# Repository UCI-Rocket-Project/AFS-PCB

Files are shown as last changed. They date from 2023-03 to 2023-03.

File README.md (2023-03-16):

# UCIRP Avionics Flight Sensor (AFS)
v1.1 "Rigel" (a star in Orion's constellation)

The board includes: 
- [Adafruit BMP388](https://www.amazon.com/Adafruit-BMP388-Precision-Barometric-Altimeter/dp/B07JXYK9ZB) Barometric and Pressure Sensor
- [Hitlego MPU-6050](https://www.amazon.com/HiLetgo-MPU-6050-Accelerometer-Gyroscope-Converter/dp/B01DK83ZYQ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) Accelerometer and Gyroscope
- [Adafruit Ultimate GPS](https://www.adafruit.com/product/746#description)
- [Digi XBee-PRO XSC S3B](https://www.mouser.com/ProductDetail/Gravitech/XBee-USB?qs=Vxac6xGyzPnMlpwH9hhfHQ%3D%3D) 
- [Sparkfun XBee Adapter](https://www.sparkfun.com/products/11373)
- Teensy 4.1
- [Linear Regulator (9V -> 5V)](https://www.digikey.com/en/products/detail/stmicroelectronics/L7805CV/585964)

Communication Protocols Used:
| Component  | Communication Protocol | 
| --- | --- |
| BMP388  | SPI  | 
| ECU 1.5 "Orion" | I2C (Wire) |
| GPS  | UART (Serial 2) |
| MPU-6050  | I2C (Wire 1)  |
| SD Module | SPI |
| XBEE  | UART (Serial 6) |

Pinouts:

BMP
- CS	 -> 10 CS
- SDI  -> 11 MOSI
- SDO  -> 12 MISO
- SCK  -> 13 SCK

ECU 1.5 "Orion"
- SDA2  -> 18 SDA
- SCL2  -> 19 SCL

GPS (Serial2 port in Teensy 4.1)
- TX	 -> 7 RX2
- RX	 -> 8 TX2

MPU (Wire1 port in Teensy 4.1)
- SDA  -> 17 SDA1
- SCL	 -> 16 SCL1

SD Module 
- MISO -> 39 MISO1
- MOSI -> 26 MOSI1
- SCK  -> 27 SCK1
- CS   -> 38 CS1

XBEE (Serial6 port in Teensy 4.1)
- DOUT -> 25  RX6
- DIN  -> 24 TX6

## Used Packages
- Teensy 4.1 [symbol](https://github.com/XenGi/teensy_library) and [footprint](https://github.com/XenGi/teensy.pretty). Related files and license is located under `/teensylib`.

## Notes
- The board requires an external 9V battery to power sensors and the Teensy. The onboard regulator will step down to 5V and provide stable 5V power.
- The GPS uses an optional "CR1220 coin cell to keep the RTC running and allow warm starts"
- The XBee module (not on AFS PCB) mounts on top of the XBee USB adapter. The USB adapter board has power and serial pass-through to the XBee module
- The board was renamed from "Avionics Test Payload (ATP)" to "Avionics Flight Sensor (AFS)"

### v1.1
- Changed [Adafruit XBee USB Adapter](https://www.adafruit.com/product/247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) to [Sparkfun XBee Adapter](https://www.sparkfun.com/products/11373)
- XBee receives 5V from regulator, instead of 3.3V from Teensy. During testing we found out that Teensy did not supply enough power for Xbee communication and after sending 1 or 2 packages of data, the Teensy would stop working.
- Regulator is flipped, so we can attach a heat sink

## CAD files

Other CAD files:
atp_teensy.wrl.SLDPRT

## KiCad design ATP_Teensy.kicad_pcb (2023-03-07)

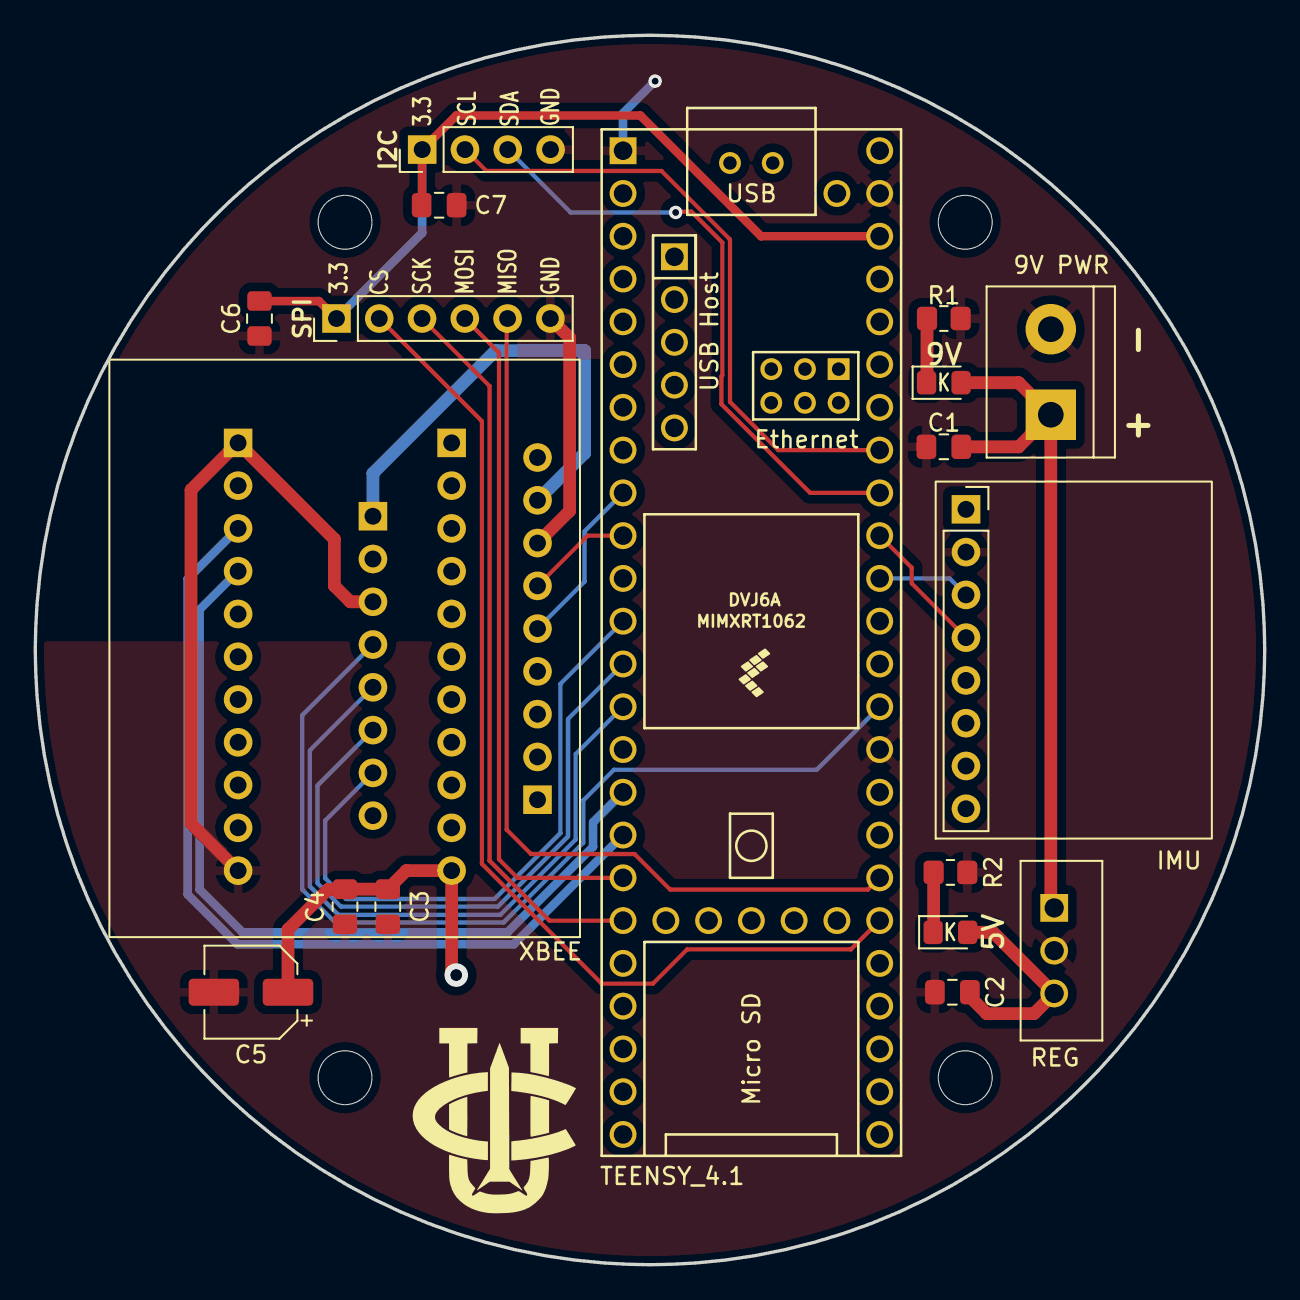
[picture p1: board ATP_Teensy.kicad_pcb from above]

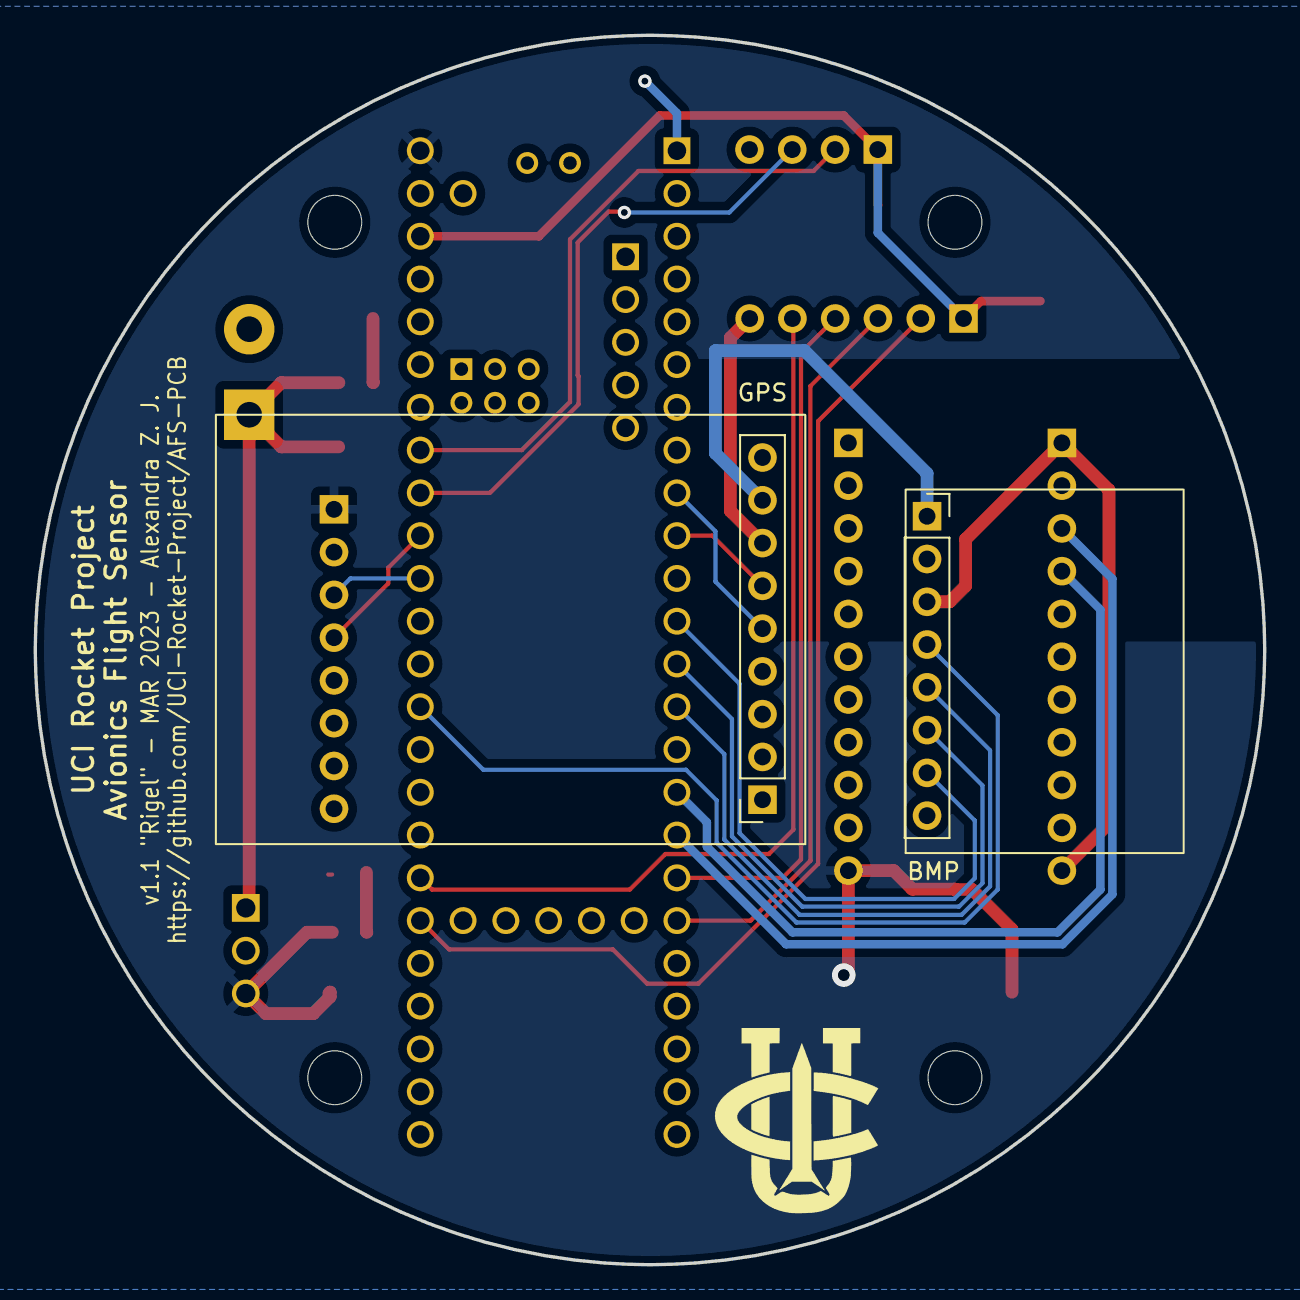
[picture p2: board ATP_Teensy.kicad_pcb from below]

Board: 2 copper layers, 73.0 x 73.0 mm, 26 parts (3 on the bottom side), 22 nets.

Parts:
5V, 9V: LED; LED_0805_2012Metric_Pad1.15x1.40mm_HandSolder
9V PWR: Screw_Terminal_01x02; TerminalBlock_bornier-2_P5.08mm
BMP: BMP388_3966; BMP_board
C1, C2: 10nF; C_0805_2012Metric_Pad1.18x1.45mm_HandSolder
C3: 47pF; C_0805_2012Metric_Pad1.18x1.45mm_HandSolder
C4, C6, C7: 1uF; C_0805_2012Metric_Pad1.18x1.45mm_HandSolder
C5: 10uF, 50V; CP_Elec_5x5.4
GPS: GPS; GPS_board
Ge: LOGO; UCIRP_logo
Ge#2: LOGO; UCIRP_logo
I2C: Conn_01x04_Male; PinHeader_1x04_P2.54mm_Vertical
IMU: MPU6050; IMU_board
J2, J3, J4, J5: Conn_01x01; MountingHole_3.2mm_M3
R1: 290R; R_0805_2012Metric_Pad1.20x1.40mm_HandSolder
R2: 90R; R_0805_2012Metric_Pad1.20x1.40mm_HandSolder
REG: L7805CV
SPI: Conn_01x06_Male; PinHeader_1x06_P2.54mm_Vertical
TEENSY_4.1: Teensy4.1; Teensy41
XBEE: XBee_SparkfunRegulatedAdapter; XBee_SparkfunAdapter

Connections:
+3.3V: C6.2, C7.2, I2C.1, SPI.1, TEENSY_4.1.46 (3V3)
+5V: 5V.2 (A), BMP.1 (VIN), C2.2, C3.2, C4.2, C5.1, GPS.8 (VIN), IMU.1 (VCC), REG.3 (OUT), TEENSY_4.1.48 (VIN), XBEE.22 (5V_IN)
+9V: 9V.2 (A), 9V PWR.1, C1.2, REG.1 (IN)
BMP_CS: BMP.7 (CS), TEENSY_4.1.12 (10_CS_MQSR)
BMP_SCK: BMP.4 (SCK), TEENSY_4.1.35 (13_SCK_LED)
BMP_SDI: BMP.6 (SDI), TEENSY_4.1.13 (11_MOSI_CTX1)
BMP_SDO: BMP.5 (SDO), TEENSY_4.1.14 (12_MISO_MQSL)
ECU_SCL: I2C.2, TEENSY_4.1.41 (19_A5_SCL)
ECU_SDA: I2C.3, TEENSY_4.1.40 (18_A4_SDA)
GND: 9V PWR.2, BMP.3 (GND), C1.1, C2.1, C3.1, C4.1, C5.2, C6.1, C7.1, GPS.7 (GND), I2C.4, IMU.2 (GND), R1.2, R2.2, REG.2 (GND), SPI.6, TEENSY_4.1.1 (GND), TEENSY_4.1.34 (GND), TEENSY_4.1.47 (GND), XBEE.1 (GND), XBEE.11 (GND)
GPS_RX: GPS.6 (RX), TEENSY_4.1.10 (8_TX2_IN1)
GPS_TX: GPS.5 (TX), TEENSY_4.1.9 (7_RX2_OUT1A)
MPU_SCL: IMU.3 (SCL), TEENSY_4.1.38 (16_A2_RX4_SCL1)
MPU_SDA: IMU.4 (SDA), TEENSY_4.1.39 (17_A3_TX4_SDA1)
unnamed: 9V.1 (K), R1.1
unnamed: 5V.1 (K), R2.1
SD_CS: SPI.2, TEENSY_4.1.30 (38_CS1_IN1)
SD_MISO: SPI.5, TEENSY_4.1.31 (39_MISO1_OUT1A)
SD_MOSI: SPI.4, TEENSY_4.1.18 (26_A12_MOSI1)
SD_SCK: SPI.3, TEENSY_4.1.19 (27_A13_SCK1)
XBEE_DIN: TEENSY_4.1.16 (24_A10_TX6_SCL2), XBEE.4 (DIN)
XBEE_DOUT: TEENSY_4.1.17 (25_A11_RX6_SDA2), XBEE.3 (DOUT)

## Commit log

2022-10-31 add footprints
    [ATP_Teensy.kicad_sch]
2022-12-03 Add LED indicators
    [ATP_Teensy.kicad_pcb, ATP_Teensy.kicad_sch]
2022-12-03 Add mounting holes
    [ATP_Teensy.kicad_pcb]
2022-12-10 Change BMP connection from I2C to SPI
    [ATP_Teensy-B_Cu.gbr, ATP_Teensy-B_Mask.gbr, ATP_Teensy-B_Paste.gbr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]
2022-12-18 Add filtering capacitors for XBee
    [ATP_Teensy-B_Cu.gbr, ATP_Teensy-B_Mask.gbr, ATP_Teensy-B_Paste.gbr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]
2022-12-18 Add notes to XBee adapter
    [ATP_Teensy.kicad_sch]
2022-12-18 Replace 10uF CER CAP with 10uF ELE CAP
    [ATP_Teensy-B_Cu.gbr, ATP_Teensy-B_Mask.gbr, ATP_Teensy-B_Paste.gbr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]
2022-12-19 Update notes on schematic
    [ATP_Teensy-B_Cu.gbr, ATP_Teensy-B_Mask.gbr, ATP_Teensy-B_Paste.gbr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]
2023-02-28 Generated 3d files of AFS
    [atp_teensy.wrl.SLDPRT]
2023-02-28 added spi and i2c connections, actual mounting holes, change xbee power input in the schematic
    [ATP_Teensy.kicad_pcb, ATP_Teensy.kicad_sch]
2023-03-06 v1.1 Layout done, change direction of reg, added spi and i2c extensions
    [ATP_Teensy.kicad_pcb, ATP_Teensy.kicad_sch]
2023-03-07 Add labels for layout, DRC run, v1.1 Gerber files generated
    [ATP_Teensy-B_Cu.gbr, ATP_Teensy-B_Mask.gbr, ATP_Teensy-B_Paste.gbr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]

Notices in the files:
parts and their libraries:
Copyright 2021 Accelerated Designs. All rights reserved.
